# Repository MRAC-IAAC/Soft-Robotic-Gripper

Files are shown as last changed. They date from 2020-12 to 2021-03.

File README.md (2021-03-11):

# Soft-Robotic-Gripper
The initial idea is to explore the state of the art in the area of soft robotics. They consist of inflatable parts that allow the flexibiity to be able to grab objects with different profiles and delicate/ fragile items. 
For the purpose of this excercise, we created a toolpath in which the soft gripper picks up a lightbulb and screws it into a desk lamp. 
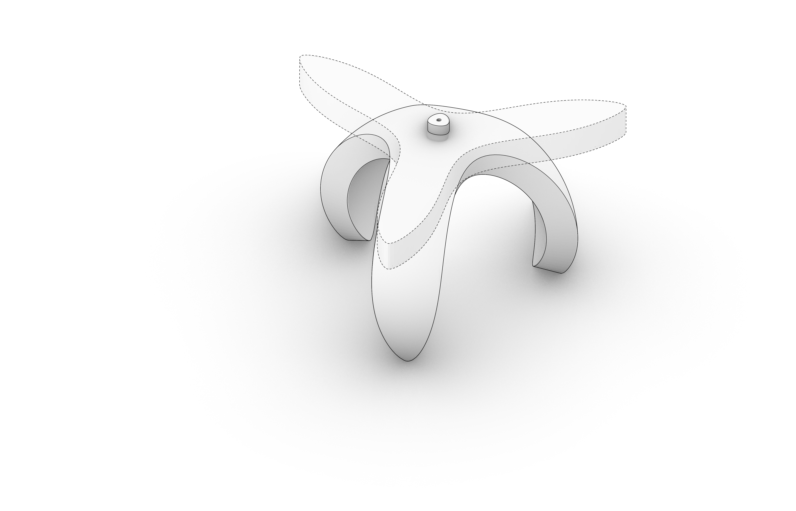
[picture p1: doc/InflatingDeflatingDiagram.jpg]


# Requirements
**3D Parts:**

**For the syringe pump assembly**

* 50cm x 60cm Acrylic sheet
* M3X16mm Screws (28)
* M3X20mm Screws (14)
* M3X6mm Screws (4)
* Silicone Tubes (Diam. depends on the syringe used)
* Syringe 100ml (2)
* 6mm Steel Rod (Circle Profile)

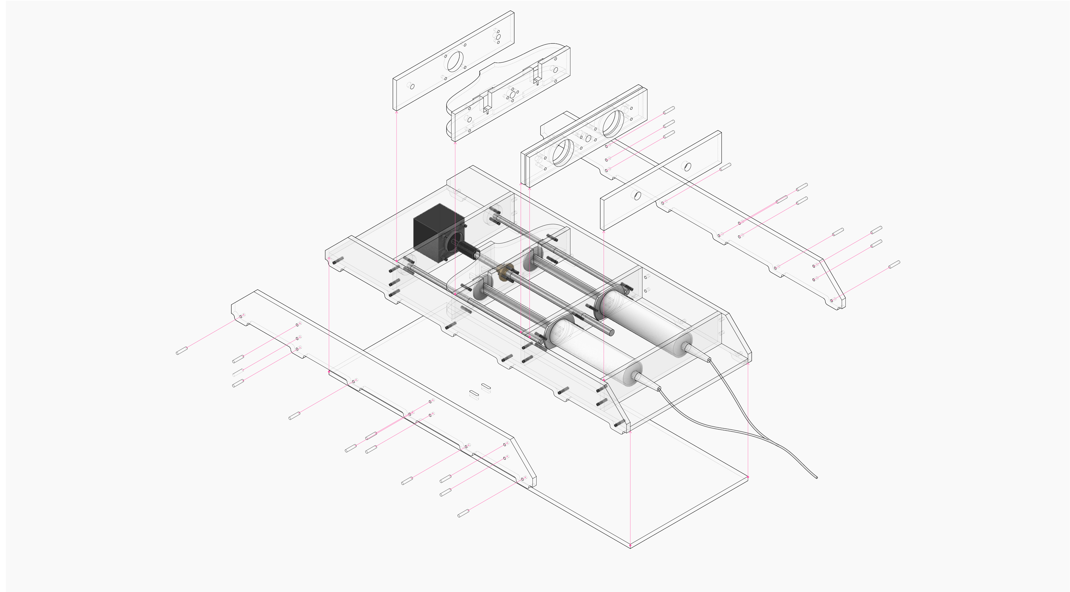
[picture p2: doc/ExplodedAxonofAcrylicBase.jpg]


**For the end effector**
* Acrylic (laser file for the end effector is placed in the same file as the acrylic base)
* EcoFlex 00-30 Silicone
* 3D Printed Mold

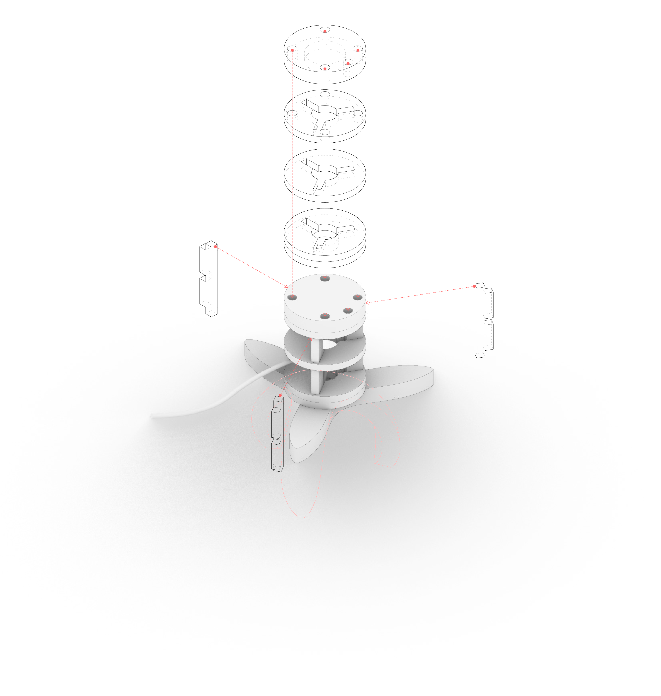
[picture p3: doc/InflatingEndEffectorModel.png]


**Electronics:**

**Parts**
  * Arduino Uno
  * Nema 17 Stepper Motor
  * Stepper Driver (A4988)
  * 100 uF Capacitor
  * 12V Power Supply
  * Bread Board
  * End Stopper Sensor
  * M8 Lead Screw 
  * 5V Power Supply
  * Optocoupler
  * Several Jumper Wires
  
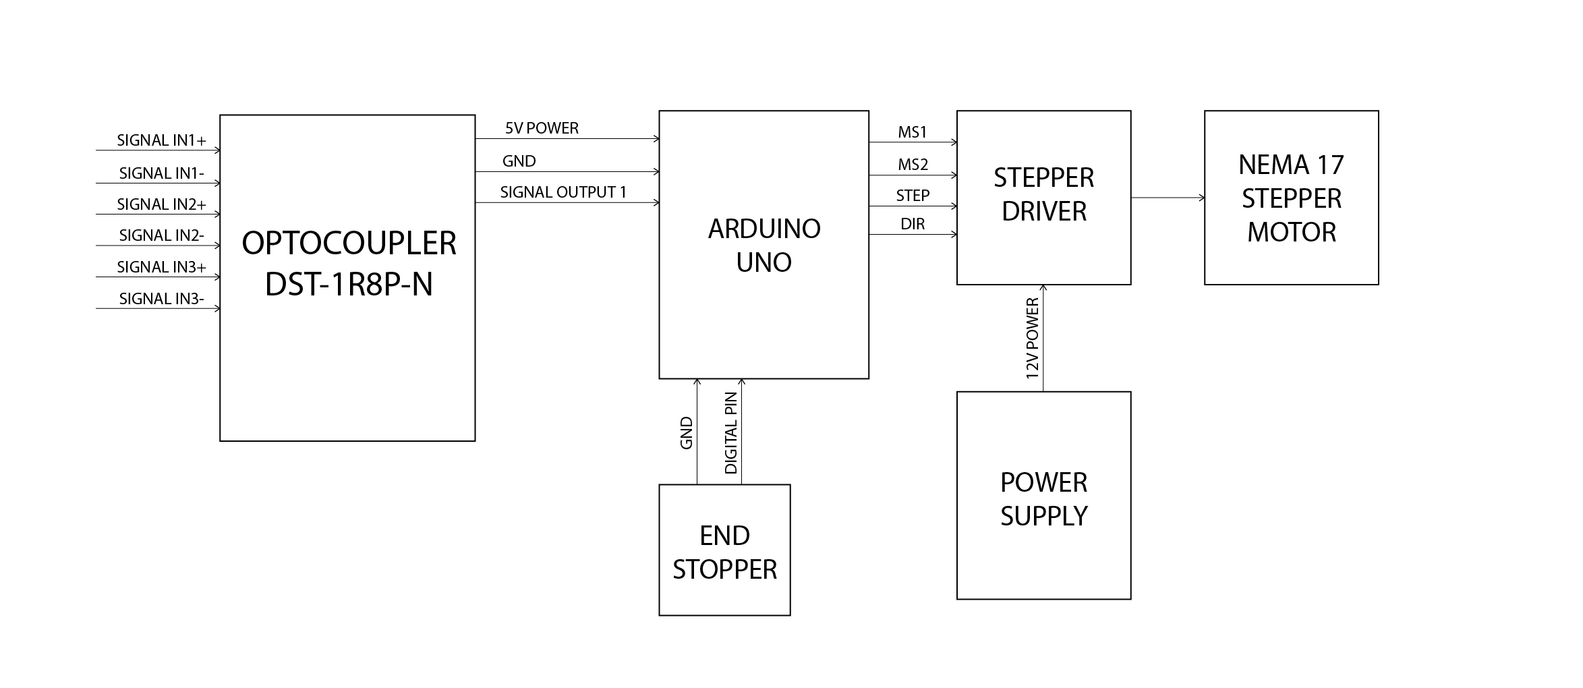
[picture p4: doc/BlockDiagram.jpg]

  
**Softwares:**
This project creates a simple syringe pump that is controlled by a stepper motor which receives signals from the optocoupler from an ABB140 Robotic Arm. A boolean statement is written within the arduino code, to determine whether the gripper inflates or deflates. 

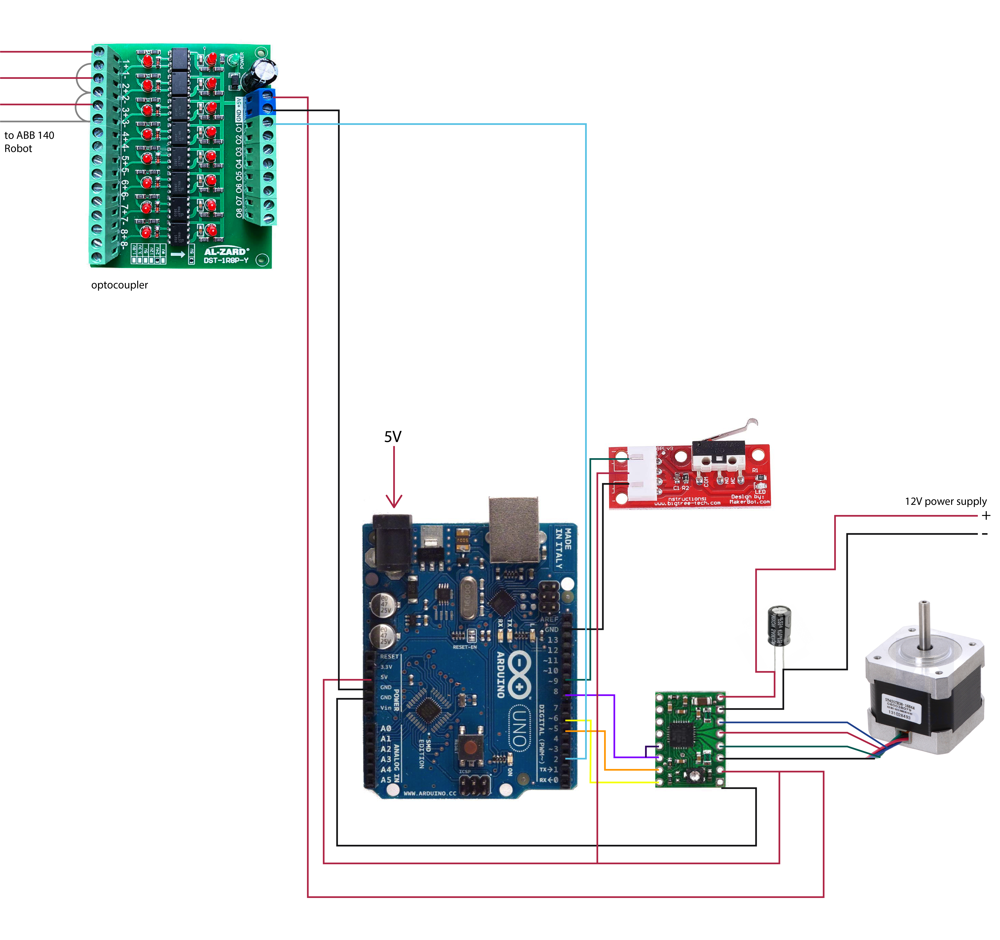
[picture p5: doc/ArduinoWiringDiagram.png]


# Getting Started
Download the arduino code

Follow the wiring diagram in order to make sure that the arduino code will be successfully uploaded into the arduino uno. Next, connect the arduino uno to the optocoupler, and the homing process that is written in the arduino code should start. The homing process identifies the starting position, once a binary signal is released from the optocoupler, the motor is triggered to turn on, therefore inflating the soft gripper. As written in the notes in the arduino code, the binary signals 0/1 determine whether the motor rotates clockwise or counter clockwise. 

# Credits
**SOFT ROBOTIC GRIPPER // HARDWARE I** is a project of IAAC, Institute for Advanced Architecture of Catalonia developed at the **Master in Robotics and Advanced Construction** in **2020/2021** by:

Students: **Hendrik Benz, Michael DiCarlo, Aslinur Taskin**

Faculty: **Angel Munoz**

Faculty Assistant: **Matthew Gordon**

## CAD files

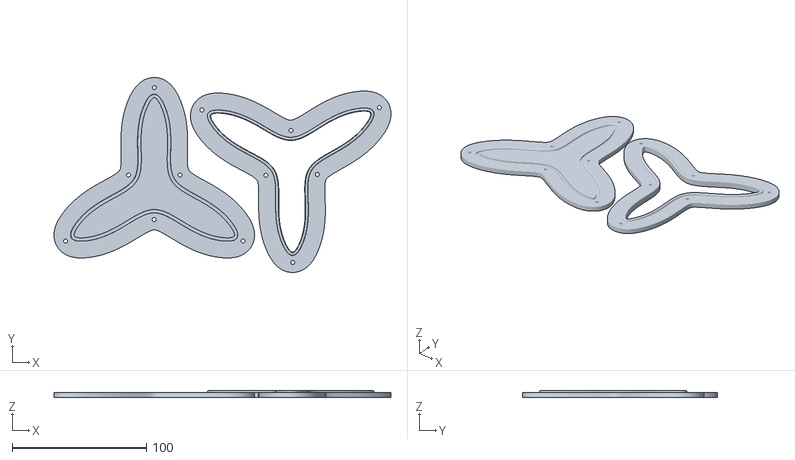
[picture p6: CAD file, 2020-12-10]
src/Hardware/Gripper Mold Bottom.stl
251.0 x 145.2 x 5.40

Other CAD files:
src/Hardware/Acrylic Base Model and Laser File.3dm

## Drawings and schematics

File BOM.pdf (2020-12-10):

Hardware | BOM

## Material needs

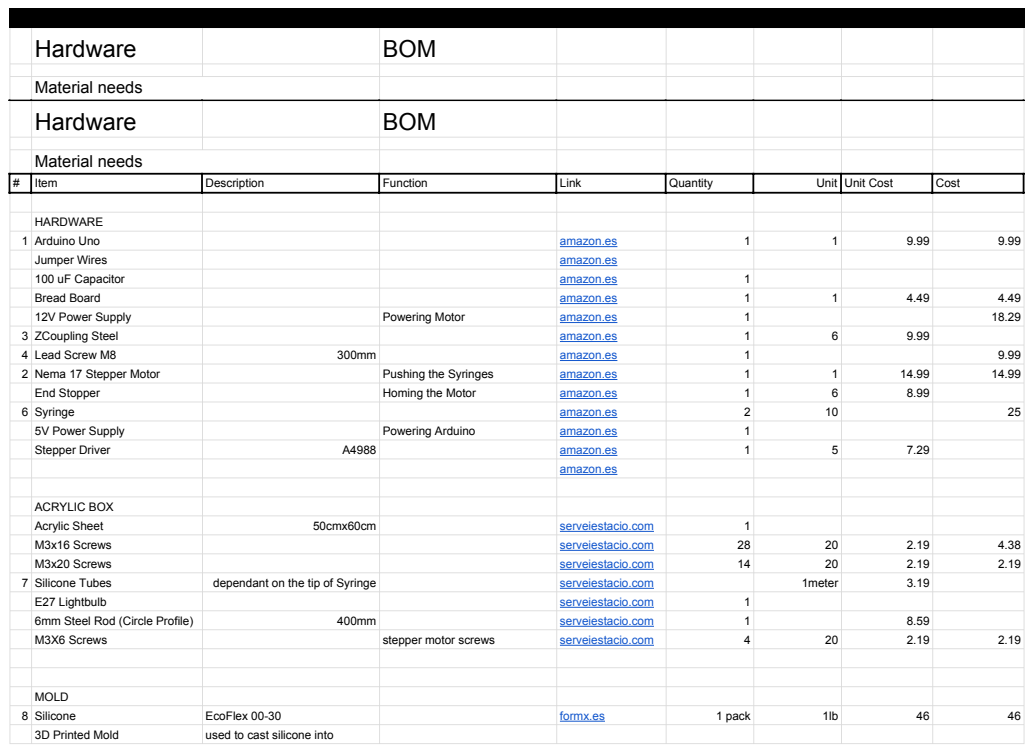
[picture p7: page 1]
Hardware; BOM; Material needs; Item; Description; Function; Link; Quantity; Unit; Unit Cost; Cost; HARDWARE; 1 Arduino Uno; amazon.es; Jumper Wires; 100 uF Capacitor; Bread Board; 12V Power Supply; Powering Motor; 3 ZCoupling Steel; 4 Lead Screw M8; 2 Nema 17 Stepper Motor; Pushing the Syringes; End Stopper; Homing the Motor; 6 Syringe; 5V Power Supply; Powering Arduino; Stepper Driver; ACRYLIC BOX; Acrylic Sheet; 50cmx60cm; serveiestacio.com; M3x16 Screws; M3x20 Screws; 7 Silicone Tubes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

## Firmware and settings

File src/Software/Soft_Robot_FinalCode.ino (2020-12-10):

int dir_pin = 6;
int step_pin = 5;
int steps = 200; //fixed number of steps per revolution for stepper motors
int uStep = 1; //revolution, should be one 
int numTurns = 12; //number of turns per revolution
int delayInc = 750; //determines the speed of the revolution
int MS1 = 10; //not connected
int MS2 = 11;  //not connected
int MS3 = 12;  //not connected
int home_switch = 9; //end stopper pin connected to arduino
int sleep_pin = 8; //making this low puts the driver to sleep, making it high awakens the driver for it to run
int steps_home;

int direction;

boolean  currentState = false; //need to define the state before the loop begins in order to understand the starting point of the loop
int robotPin = 2; //pin in arduino from optocouplet connected to the robot

void setup() { //set the pinModes to output
  pinMode(MS1, OUTPUT);
  pinMode(MS2, OUTPUT);
  pinMode(dir_pin, OUTPUT);
  pinMode(step_pin, OUTPUT);
  pinMode(sleep_pin, OUTPUT);
  pinMode(robotPin, INPUT);
  pinMode(home_switch, INPUT_PULLUP);

  currentState = digitalRead(robotPin);

  digitalWrite(sleep_pin, HIGH);  // Wake up stepperDriver
  delay(5);  // Wait for Driver wake up
  Serial.begin(9600);

  /* LOW LOW = Full Step //
    // HIGH LOW = Half Step //
    // LOW HIGH = A quarter of Step //
    // HIGH HIGH = An eighth of Step //
  */
  digitalWrite(MS1, LOW);      // Configures to Full Steps
  digitalWrite(MS2, LOW);    // Configures to Full Steps
  digitalWrite(MS3, LOW);     // Configures to Full Steps
  // Start Homing procedure of Stepper Motor at startup:

  while (digitalRead(home_switch)) {  // Do this until the switch is activated
    digitalWrite(dir_pin, LOW);      // (HIGH = anti-clockwise / LOW = clockwise)
    digitalWrite(step_pin, LOW);
    delay(5);                       // Delay to slow down speed of Stepper
    digitalWrite(step_pin, HIGH);
    delay(5);
  }

  while (!digitalRead(home_switch)) { // Do this until the switch is not activated
    digitalWrite(dir_pin, HIGH);
    digitalWrite(step_pin, HIGH);
    delay(5);                       // More delay to slow even more while moving away from switch
    digitalWrite(step_pin, LOW);
    delay(5);
  }

  steps_home = 0; // Reset position variable to zero

  Serial.println("Homing done");

}
void loop() {
  boolean robotInput = !digitalRead(robotPin);  //0 FALSE (BACKWARD), 1 TRUE (FORWARD)
  Serial.println(digitalRead(robotPin));

  if (robotInput && currentState == true) {
    digitalWrite(dir_pin, HIGH);
    for (long i = 0; i < steps * uStep * numTurns; i++) {
      digitalWrite(step_pin, HIGH);
      delayMicroseconds(delayInc * 2);
      digitalWrite(step_pin, LOW);
      delayMicroseconds(delayInc * 2);
    } // motor loop
    currentState = false;
  }

  if (robotInput == 0 && currentState == false) {
    digitalWrite(dir_pin, LOW);

    for (long i = 0; i < steps * uStep * numTurns; i++) { //
      digitalWrite(step_pin, HIGH);
      delayMicroseconds(delayInc * 2);
      digitalWrite(step_pin, LOW);
      delayMicroseconds(delayInc * 2);
    }

    // motor loop
    currentState = true;
  }
}
